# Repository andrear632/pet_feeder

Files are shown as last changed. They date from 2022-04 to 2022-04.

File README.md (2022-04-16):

# Pet Feeder
*Individual project for the IoT course 2022 at La Sapienza University of Rome*

The project was born from the need to feed my pet automatically or manually from remote places. To solve that problem I created a cloud-based IoT system that collects information from sensors and interacts with the environment using actuators.

## Architecture
The IoT device is developed using RIOT-OS and a STM NUCLEO-f401re board. The cloud-based services are based on the AWS ecosystem.
The system includes two sensors and two actuators:
- Ultrasonic sensor (HC SR04): measures the fill level of the dispenser. It is put on top of the food container and measures the distance from the food. While it is dispensed, the level goes down and the ultrasonic measures bigger distances.
After it has been activated, this sensor returns an echo back whose pulse width (uS) is proportional to the distance measured. This value can be divided by 58 to obtain the distance in cm. The resolution is 0.3cm and the minimum distance that can be measured is 2cm. For that reason, the sensor was placed 2cm above the maximum fill level of the food container.
When the container is empty the sensor is going to measure the distance from the screw. This distance will depend on the current rotation position of the screw, so values bigger than the threshold (5.69cm - 330uS) will be considered as empty level. The container will be considered filled when the sensor measures a distance equal to 2.59cm (150uS).
- PIR motion sensor (HC SR501): check if the pet is walking past the food dispenser. This sensor is always on. When it detects movements inside the range of a 110° angle and 5m distance, a 3.3V impulse of 3 seconds is sent to the analog pin. Every second the value emitted by the sensor is read from the board and if it is high (it has detected movements) it triggers the stepper motor.
- Stepper motor (28BYJ 48 + ULN 2003 driver): rotates a screw which dispenses the food.
- Led: lights on when the food container is empty.

The board is connected through MQTT-SN to a broker hosted on the machine the board is connected to. The connection is carried out using IPv6 and RIOT-OS tap interfaces. The board publishes on “topic_out” and subscribes to “topic_in” to receive messages from outside.

A transparent bridge written in python is used to forward messages to and from AWS IoTCore. It runs on the machine the board is connected to. It reads messages from the local broker with “topic_out” and publishes them to AWS IoTCore on the same topic. It also reads messages from AWS IoTCore with “topic_in” and publishes them on the local broker with the same topic.

Once data arrives to AWS IoTCore the computation proceeds on the AWS cloud using the following services: DynamoDB, Lambda, API Gateway, Amplify.

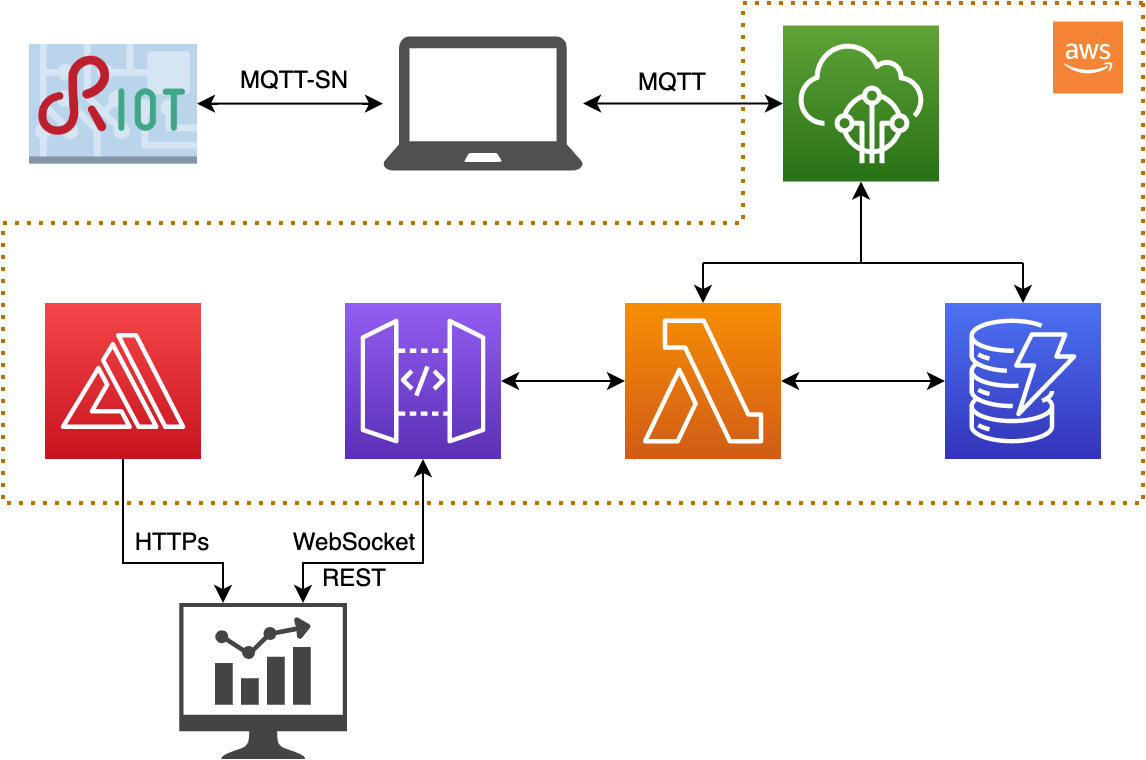
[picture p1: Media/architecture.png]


## Network
In the network there will be transmitted only the fill level coming from the board and the dispense message going to the board. These messages are less than 10 bytes, so even a narrow band will be suitable for our use. Low latency is required to deliver the dispense message, as the user expects its action of clicking the button on the web dashboard to be executed in the range of 1 to 5 seconds.
- The average measured latency of the system from the moment in which the ultrasonic sensor is asked to read the fill level to the point in which the result is integrated in the dashboard is less than 2 seconds. That is also because of the time the browser takes to update after it receives a message from the WebSocket.
- The average measured latency of the system from the moment in which the user requests a dispense from the dashboard to the point in which the stepper motor actually dispenses food is less than 1 second.
- The average round trip time from the moment in which the user requests a dispense from the dashboard to the point in which the new fill level is integrated in the dashboard is less than 7 seconds. That is because the fill level is measured after the dispenser has finished dispensing food and this process lasts 4 seconds.

These latencies are short enough to not affect the usability of the system and are compliant with the objectives set before the development.

Data is transmitted every time the user asks to dispense food and every time food is dispensed (to store the fill level in the cloud). In the first case the message will have a fixed length of 8 bytes. In the second case the message will have a fixed length of 3 bytes. Clearly there will be overhead due to headers necessary to transmit the messages. MQTT-SN was chosen as the protocol to transmit messages because of its characteristics suitable for IoT applications, in particular for its small overhead.

Here are some more precise results obtained using wireshark:
- When the user asks to dispense from the web dashboard, there is only one incoming packet to the board of total size 77 bytes.
- When the board needs to communicate to the broker the fill level, it outputs a first packet of size 77 bytes containing the topic, the broker answers with a 69 bytes packet and finally the board sends the fill level in a packet of total size 72 bytes.

## Logic
This IoT system follows the 'Sense-Think-Act' paradigm.

When the PIR motion sensor detects a pet walking past the dispenser it sends an impulse to an analog pin which is read every second. When the impulse is detected a callback function is called and the stepper motor is activated to do 2000 steps and dispense food. A timer is set to disable the stepper for a certain amount of time and avoid it dispensing food every time the pet walks past. The user can also dispense food from remotely using a web dashboard.

After having dispensed food, the ultrasonic sensor is activated to measure the fill level of the food container. If the value is over a threshold the led is switched on to report that it needs to be filled. If the led is on but the container has been filled, it is switched off.

The application collects and stores only the fill level coming from the ultrasonic sensor. This happens after every time food is dispensed, both if as a consequence of motion detection or if the user has manually dispensed it. These data are then stored in AWS DynamoDB to be included in the web dashboard.

The computation linked to sensors and actuators is carried on entirely on the board. This choice was made because the board could provide the required computational power and it avoided higher latencies to send data to the cloud and retrieve the instructions to be performed. This choice also reduced the number of messages exchanged over the network and the cloud usage.

The cloud only manages the communications with the user via the web dashboard. The following AWS services were used:

DynamoDB:
- table: connections; partition key: conn_id (String).
- table: pet_feeder; partition key: id_time (Number); column: fill_level (String).

API Gateway:
- name: update_level; protocol: WebSocket; routes: connect (linked to lambda function websocket_connect.py) and disconnect (linked to lambda function websocket_disconnect.py).
- name: petfeeder_api; protocol: REST; resources: GET (linked to lambda function read_level_from_db.py) and POST (linked to lambda function publish_dispense_to_iotcore.py).

AWS Amplify:
- Code inside WebApp folder.

IoTCore:
- rule: perfeeder_store; rule query statement: SELECT message FROM 'topic_out'; actions:
Insert a message into a DynamoDB table (partition key value: ${timestamp()}; write message data to this column: fill_level) and
Send a message to a lambda function (send_to_websocket.py).
- messages format: topic_in {“message” : “dispense”}; topic_out {“message” : “%value”} where %value is an integer.

Lambda functions:
- publish_dispense_to_iotcore: publishes the dispense message to topic_in.
- read_level_from_db: returns the elements from DynamoDB table “pet_feeder” whose id_time is not older than one hour before when it is called.
- send_to_websocket: sends the new value to all active WebSocket connections.
- websocket_connect: stores in DynamoDB table “connections” the connection id in input.
- websocket_disconnect: deletes from DynamoDB table “connections” the connection id in input.

Policies were set up using AWS IAM (Identity and Access Management) to ensure proper communication between the above services.

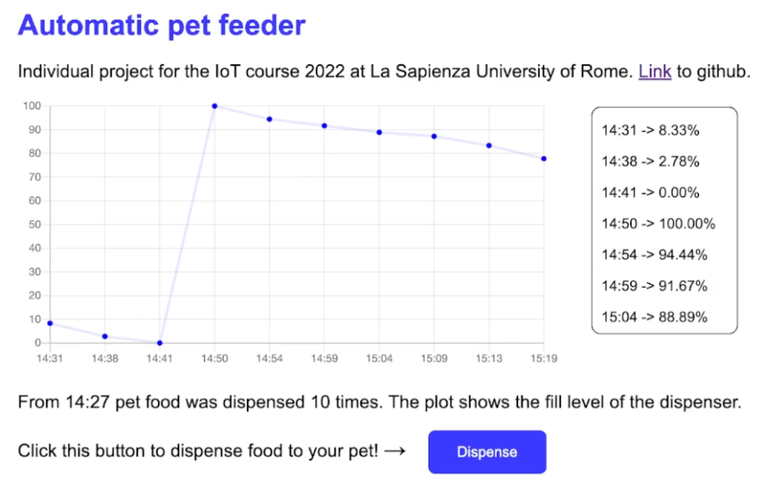
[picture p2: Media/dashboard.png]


## How to setup and run the system

1. Configure the AWS cloud system:
- Lambda. Create five lambda functions in python using the code provided in the folder LambdaFunctions. The functions are: publish_dispense_to_iotcore, read_level_from_db, send_to_websocket, websocket_connect, websocket_disconnect.
- DynamoDB. Create two tables: connections (with partition key “conn_id” of type String) and pet_feeder (with partition key “id_time” of type Number).
- IoTCore. Create a new Thing. Then set up a new rule using the selector “SELECT message FROM 'topic_out'” and two actions: insert message in DynamoDB table (with partition key value “${timestamp()}” and write message data to the column “fill_level”) and sends a message to the lambda function “send_to_websocket.py”.
- API Gateway. Create a REST API with resources GET (linked to lambda function read_level_from_db.py) and POST (linked to lambda function publish_dispense_to_iotcore.py). Create a WebSocket API with routes “connect” (linked to lambda function websocket_connect.py) and “disconnect” (linked to lambda function websocket_disconnect.py). Inside the lambda function send_to_websocket.py update the endpoint url with the one provided by the API gateway.
- Amplify. Create a new app and upload the code provided in the WebApp folder. In the file index.js update the API endpoints into the functions webSocketLaunch, dispense and callApi.
- IAM. Set up all the policies needed to allow the services to communicate between them.

2. Connect all the sensors and actuators to the board using the following schema:
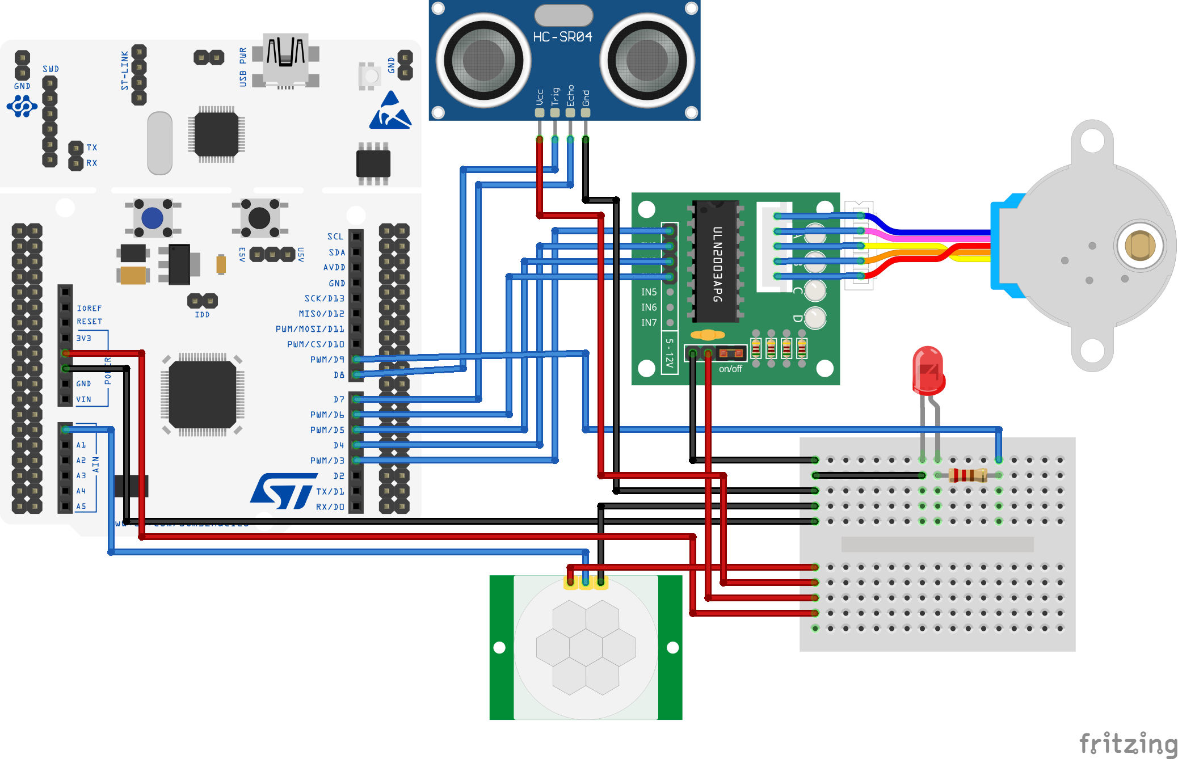
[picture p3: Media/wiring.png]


3. Clone the [mosquitto.rsmb repository](https://github.com/eclipse/mosquitto.rsmb.git) to your machine, go inside the folder mosquitto.rsmb/rsmb/src and compile the code using the command “make”. In the folder mosquitto.rsmb/rsmb create a file called config.conf and paste inside it the following code:
`listener 1885 INADDR_ANY mqtts \n ipv6 true \n listener 1886 INADDR_ANY \n ipv6 true`.
In the folder mosquitto.rsmb/rsmb launch the command “./src/broker_mqtts config.conf” to open the local MQTT broker.

4. Inside the file transparent_bridge.py configure the following parameters: host, rootCAPath, certificatePath, privateKeyPath. You should download the necessary files from AWS IotCore. Launch the transparent bridge using the command “python3 transparent_bridge.py”.

5. Clone the [RIOT repository](https://github.com/RIOT-OS/RIOT.git) to your machine and put it inside our RiotCode folder. You can adjust the time between automatic dispensing by modifying the defined value of `INTERVAL` in the file “main.c”. Then connect the board to the machine and launch the command “make flash” to compile the code and upload it to the MCU. On the machine launch the command "sudo ip a a 2000:2::1 dev tap0" (You can automate this step by inserting the same command inside the function create_tap() in RIOT/dist/tools/ethos/start_network.sh). Restart the board through the reset button.

6. Open the Web App at the link provided by AWS Amplify and use the system!

## Miscellaneous
Some 3D models for printed parts were taken from the following links:
- https://www.thingiverse.com/thing:3051036
- https://www.thingiverse.com/thing:548975
- https://www.thingiverse.com/thing:14452

Two accessories were designed specifically for this project. All 3D models can be found in the 3D folder.

[Here](https://youtu.be/5z9hatsKNmI/) you can find a video demonstration of the final system.

[Here](https://www.hackster.io/andrear632/automatic-pet-feeder-0c2639) there's a blog post related to this project.

[Here](https://dev.d26dl44y42s2gz.amplifyapp.com) you can find the dashboard.

Check [here](https://www.linkedin.com/in/andrea-rod) my LinkedIn account!

## Gallery

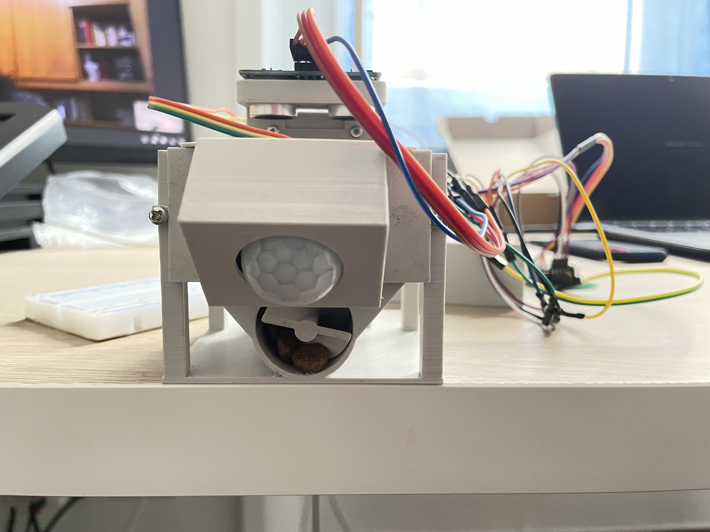
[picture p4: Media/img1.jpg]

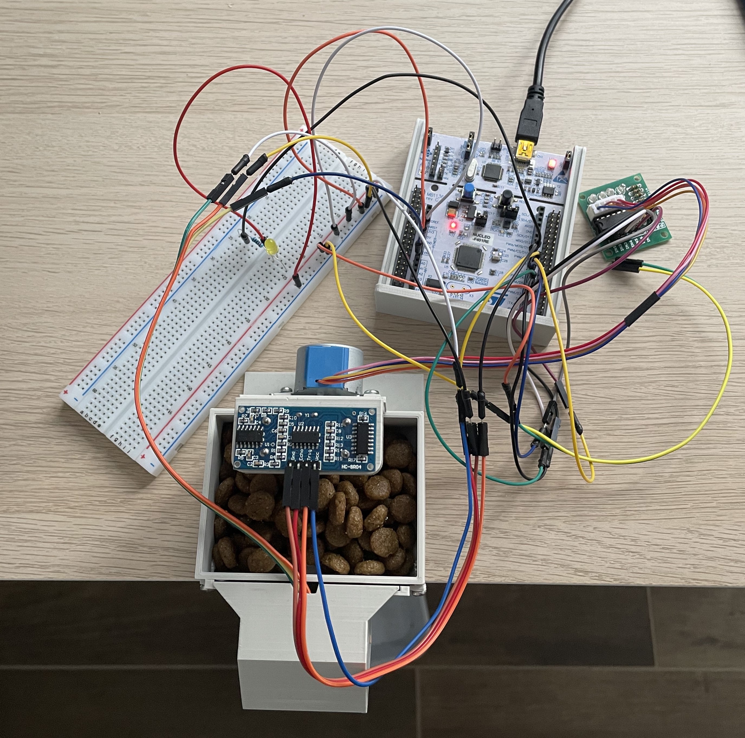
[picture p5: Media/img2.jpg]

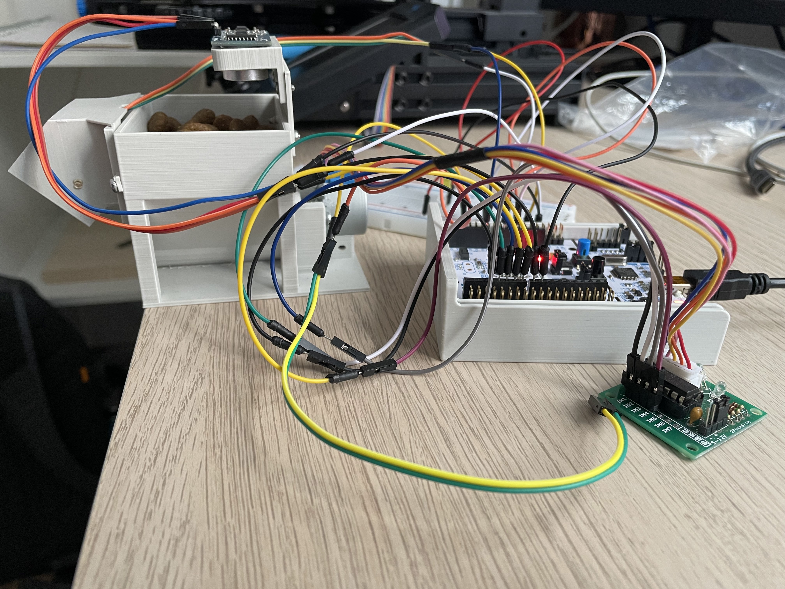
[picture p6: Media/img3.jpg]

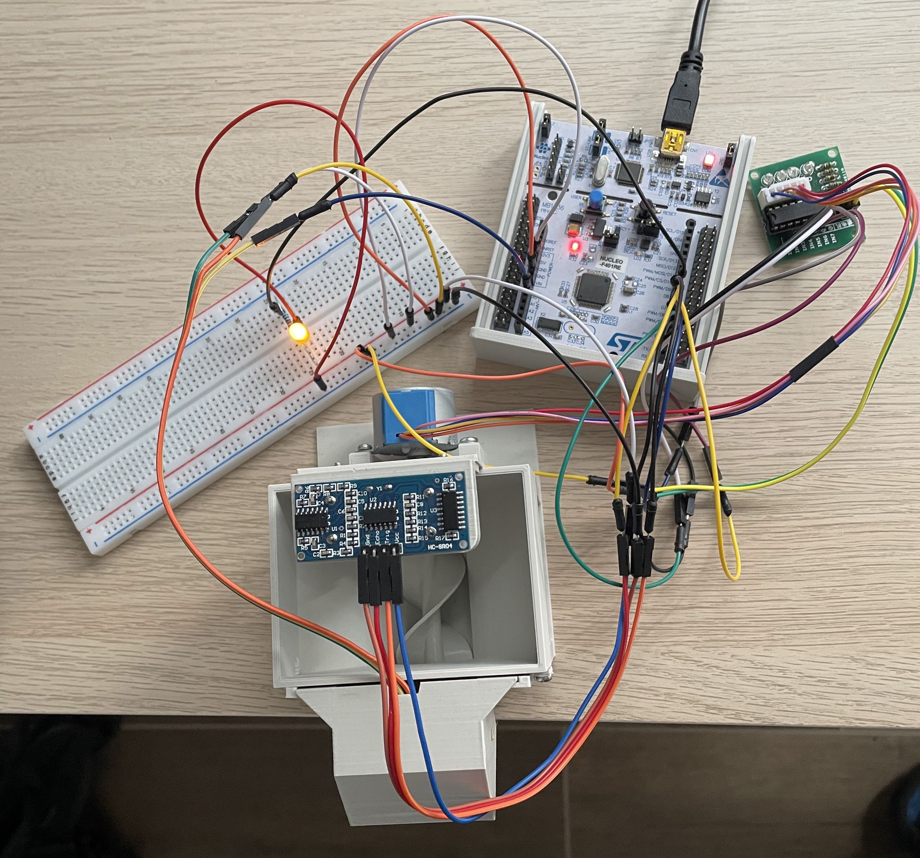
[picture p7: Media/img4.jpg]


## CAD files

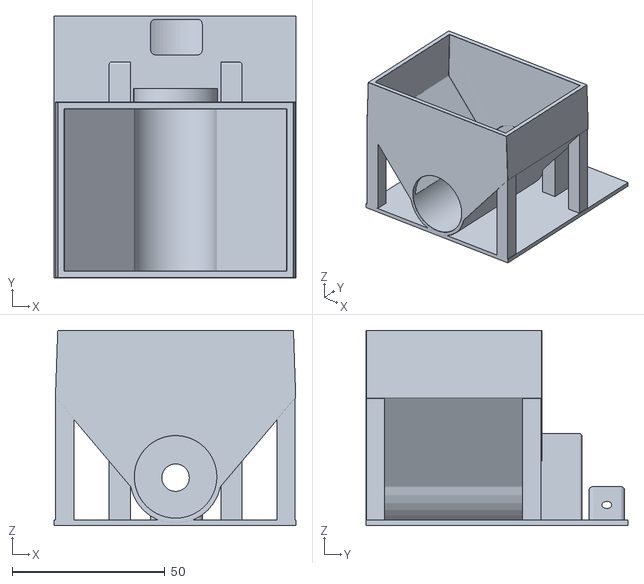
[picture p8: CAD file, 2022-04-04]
3D/whole.stl
79.1 x 85.7 x 63.9

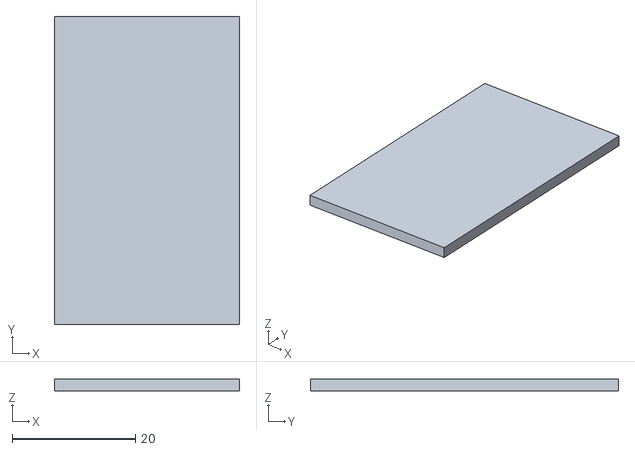
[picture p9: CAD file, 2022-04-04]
3D/accessories_ULTRASONIC.stl
30.0 x 50.0 x 2.00

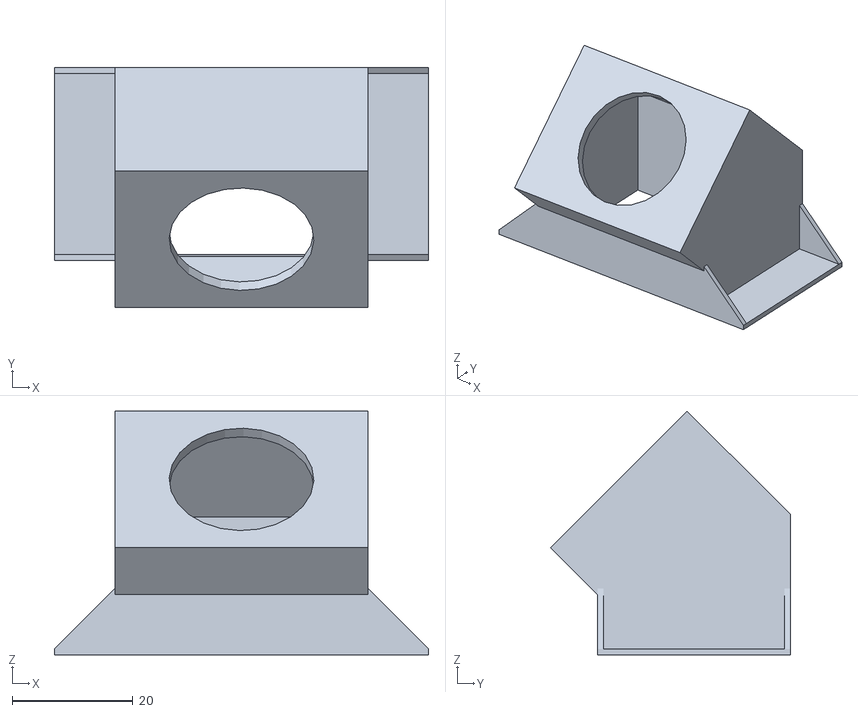
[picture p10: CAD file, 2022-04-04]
3D/box_PIR.stl
62.0 x 39.8 x 40.4

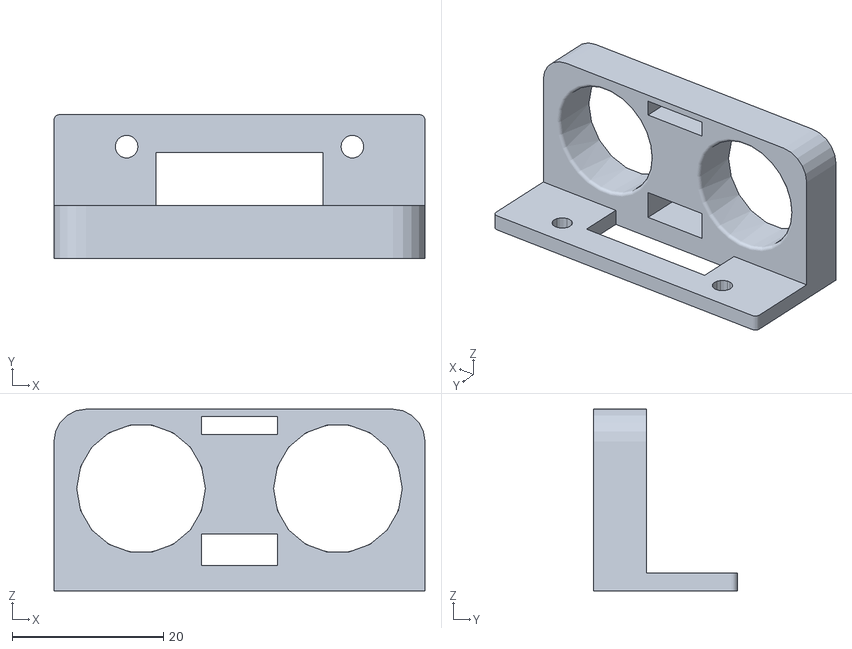
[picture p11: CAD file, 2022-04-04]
3D/box_ULTRASONIC.stl
49.0 x 19.0 x 24.0

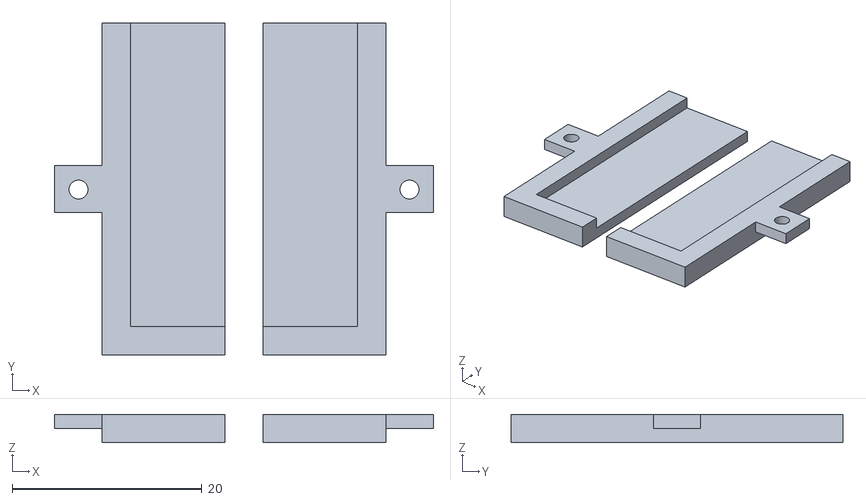
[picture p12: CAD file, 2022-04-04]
3D/accessories_PIR.stl
40.0 x 35.0 x 3.00

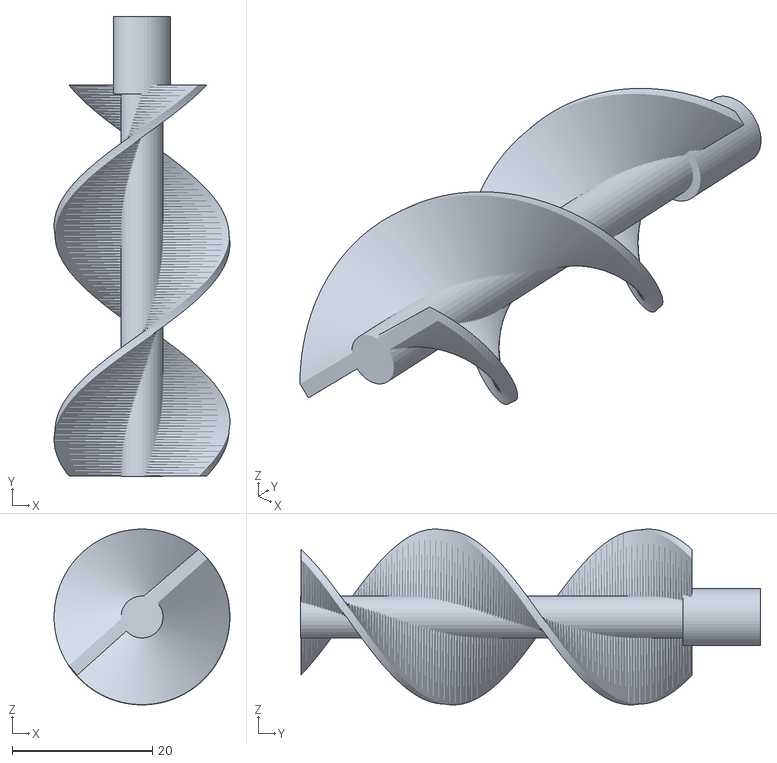
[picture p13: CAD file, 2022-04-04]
3D/screw.stl
25.1 x 65.7 x 25.1

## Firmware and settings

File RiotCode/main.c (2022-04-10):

// Local broker:
// in mosquitto.rsmb/rsmb launch "./src/broker_mqtts config.conf"
//
// Transparent bridge:
// Launch "python3 transparent_bridge.py"

#include <stdio.h>
#include <stdlib.h>
#include <string.h>
#include "msg.h"
#include "net/emcute.h"
#include "net/ipv6/addr.h"
#include "periph/gpio.h"
#include "xtimer.h"
#include "thread.h"
#include "periph/adc.h"
#include "main.h"

#define RES ADC_RES_8BIT
#define INTERVAL 10*1000000 //usec
#define EMCUTE_PRIO         (THREAD_PRIORITY_MAIN - 1)
#define _IPV6_DEFAULT_PREFIX_LEN        (64U)
#define BROKER_PORT         1885
#define BROKER_ADDRESS      "2000:2::1"
#define TOPIC_RECEIVE       "topic_in"
#define TOPIC_SEND          "topic_out"

//to add addresses to board interface
extern int _gnrc_netif_config(int argc, char **argv);

//pins stepper motor
gpio_t pin_step_1 = GPIO_PIN(PORT_B, 3); //D3 -> IN1
gpio_t pin_step_2 = GPIO_PIN(PORT_B, 5); //D4 -> IN2
gpio_t pin_step_3 = GPIO_PIN(PORT_B, 4); //D5 -> IN3
gpio_t pin_step_4 = GPIO_PIN(PORT_B, 10); //D6 -> IN4

//pins ultrasonic sensor
gpio_t trigger_pin = GPIO_PIN(PORT_A, 9); //D8 -> trigger
gpio_t echo_pin = GPIO_PIN(PORT_A, 8); //D7 -> echo

//pin PIR
//A0 -> PIR out

//pin led
gpio_t led_pin = GPIO_PIN(PORT_C, 7); //D9 -> resistor -> longled

//ultrasonic sensor
uint32_t echo_time;
uint32_t echo_time_start;

//mqtts
static char stack[THREAD_STACKSIZE_DEFAULT];
static msg_t queue[8];
static emcute_sub_t subscriptions[1];
static char topics[1][64U];

//1 if fill level alarm is triggered, 0 otherwise
int alarm_triggered = 0;
//1 if it can dispense, 0 if it is busy dispensing
int can_dispense = 1;
//1 if check_level() needs to be run, 0 otherwise
int need_check = 0;

// *** \/ MQTTS \/ ***

static void *emcute_thread(void *arg){
    (void)arg;
    emcute_run(BROKER_PORT, "board");
    return NULL;
}

static int con(void){
    sock_udp_ep_t gw = { .family = AF_INET6, .port = BROKER_PORT };
    char *topic = NULL;
    char *message = NULL;
    size_t len = 0;

    ipv6_addr_from_str((ipv6_addr_t *)&gw.addr.ipv6, BROKER_ADDRESS);
    emcute_con(&gw, true, topic, message, len, 0);

    return 0;
}

static int pub(char* msg){
    emcute_topic_t t;
    unsigned flags = EMCUTE_QOS_0;
    t.name = TOPIC_SEND;

    emcute_reg(&t);
    emcute_pub(&t, msg, strlen(msg), flags);

    return 0;
}

static void on_pub(const emcute_topic_t *topic, void *data, size_t len){
    (void)topic;

    char *in = (char *)data;
    char msg[len+1];
    strncpy(msg, in, len);
    msg[len] = '\0';
    if (strcmp(msg, "dispense") == 0){
        dispense();
    }
}

static int sub(void){
    unsigned flags = EMCUTE_QOS_0;
    subscriptions[0].cb = on_pub;
    strcpy(topics[0], TOPIC_RECEIVE);
    subscriptions[0].topic.name = topics[0];
    
    emcute_sub(&subscriptions[0], flags);

    return 0;
}

static int add_address(char* addr){
    char * arg[] = {"ifconfig", "4", "add", addr};
    return _gnrc_netif_config(4, arg);
}

// *** /\ MQTTS /\ ***


void echo_cb(void* arg){ //callback function - ultrasonic sensor
	int val = gpio_read(echo_pin);
	uint32_t echo_time_stop;

    (void) arg;

	if(val){
		echo_time_start = xtimer_now_usec();
	}
    else{
		echo_time_stop = xtimer_now_usec();
		echo_time = echo_time_stop - echo_time_start;
	}
}

void dispense(void){ //stepper motor
    if (can_dispense) {
        can_dispense = 0;
        int steps = 0;
        int count = 2000;
        while (count) {
            switch(steps) {
                case 0:
                gpio_clear(pin_step_1);
                gpio_clear(pin_step_2);
                gpio_clear(pin_step_3);
                gpio_set(pin_step_4);
                break;
                case 1:
                gpio_clear(pin_step_1);
                gpio_clear(pin_step_2);
                gpio_set(pin_step_3);
                gpio_clear(pin_step_4);
                break;
                case 2:
                gpio_clear(pin_step_1);
                gpio_set(pin_step_2);
                gpio_clear(pin_step_3);
                gpio_clear(pin_step_4);
                break;
                case 3:
                gpio_set(pin_step_1);
                gpio_clear(pin_step_2);
                gpio_clear(pin_step_3);
                gpio_clear(pin_step_4);
                break;
            } 
            steps++;
            xtimer_msleep(2);
            if (steps>3){
                steps=0;
            }
            count--;
        }
        gpio_clear(pin_step_1);
        can_dispense = 1;
        need_check = 1;
    }
}

int read_distance(void){ //ultrasonic sensor
	echo_time = 0;
	gpio_clear(trigger_pin);
	xtimer_usleep(20);
	gpio_set(trigger_pin);
	xtimer_msleep(100);
	return echo_time;
}

int read_pir(void){ //PIR sensor
    int sample = 0;
    sample = adc_sample(ADC_LINE(0), RES);
    return sample;
}

void check_level(void){ //checks the fill level and sends it to the cloud
    int distance = read_distance(); //150 means full, >330 means empty, >300 means almost empty
    char msg[4];
    sprintf(msg, "%d", distance);
    pub(msg);
    if (alarm_triggered == 0 && distance >= 300){
        gpio_set(led_pin);
        alarm_triggered = 1;
    }
    else if (alarm_triggered == 1 && distance < 300){
        gpio_clear(led_pin);
        alarm_triggered = 0;
    }
}

void sensor_init(void){ //initializes all the pins
    gpio_init(pin_step_1, GPIO_OUT);
    gpio_init(pin_step_2, GPIO_OUT);
    gpio_init(pin_step_3, GPIO_OUT);
    gpio_init(pin_step_4, GPIO_OUT);

    gpio_init(trigger_pin, GPIO_OUT);
    gpio_init_int(echo_pin, GPIO_IN, GPIO_BOTH, &echo_cb, NULL); //imposta callback quando riceve input

    adc_init(ADC_LINE(0));

    gpio_init(led_pin, GPIO_OUT);

    read_distance(); //first read returns always 0
}

void mqtts_init(void){ //initializes the connection with the MQTT-SN broker
    msg_init_queue(queue, ARRAY_SIZE(queue));
    memset(subscriptions, 0, (1 * sizeof(emcute_sub_t)));
    thread_create(stack, sizeof(stack), EMCUTE_PRIO, 0, emcute_thread, NULL, "emcute");
    
    char * addr1 = "2000:2::2";
    add_address(addr1);
    char * addr2 = "ff02::1:ff1c:3fba";
    add_address(addr2);
    char * addr3 = "ff02::1:ff00:2";
    add_address(addr3);

    con();
    sub();
}

int main(void){
    xtimer_sleep(3);
    sensor_init();
    mqtts_init();

    uint32_t dispensed_time = -1 * INTERVAL;
    
    while (true) { //continuously reads the PIR value and dispenses food if needed
        if (read_pir()>128 && xtimer_now_usec() > dispensed_time + INTERVAL){
            dispense();
            dispensed_time = xtimer_now_usec();
        }
        if (need_check){
            check_level();
            need_check = 0;
        }
        xtimer_sleep(1);
    }

    return 0;
}
